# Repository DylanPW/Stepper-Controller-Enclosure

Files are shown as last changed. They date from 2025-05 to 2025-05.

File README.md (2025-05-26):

# Stepper Controller Enclosure
CAD Files & Arduino Code for a 3D Printed Enclosure for the ZK-SMC02 Stepper Driver. Features current and voltage monitoring.

Uses an Arduino Nano, 70x40 0.42" I2C LCD, ACS712 Voltage Sensor (30A in my case), and a voltage sensor module.

Voltage and current measurements were fine for my purposes but were still inaccurate compared to my multimeter. You get what you pay for.

Enclosure fits the Stepper Controller unit, and a 5x7cm proto-pcb with screw terminals, JST-XH and header pins exposed. There is a slot for a label. STEP file is included as other hardware will require remixing.

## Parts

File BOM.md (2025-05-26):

BOM

|Item|QTY|Notes|
|---|---|---|
|ZK-SMC02|1| |
|Arduino Nano w/ headers|1| |
|5x7cm 2.54mm Proto-PCB|1|Hole spacing specific to the generic green type|
|ACS712 Current Sensor|1|30A version used here, though 5A variant would suit better. Reccommend calibrating sensor regardless in the Arduino code|
|Smart Electronics DC 0-25V Voltage Sensor|1|Remove screw terminal|
|0.42" I2C OLED (72x40) SSD1306|1|Requires mounting points in the PCB|
|54x9x2mm Clear Acrylic|1|Easily replaced, adjust retainer to suit what you have.|
|KF-301 4P Terminal Block Connector|1|I used 2x 2P connectors, 4P would be better|
|JST-XH 2P Socket|1| |
|JST-XH 2P Connector & Pins|1| |
|JST-XH 4P Socket|2| |
|JST-XH 4P Right Angle Socket|1|Used for LCD, can be substituted for standard right angle header.|
|JST-XH 4P Connector & Pins|3| |
|3 pin 2.54mm header|3|Two used for voltage sensor mounting, one of those will need the center pin removed.|
|3 pin 2.54mm Female Dupont Connector & pins|2| |
|4 pin 2.54mm header|1| |
|XT60E-M|1| |
|15 pin 2.54mm Female header|2| |
|M2x6mm Self Tapping Screws|7| |
|M2x10mm Self Tapping Screws|7| |
|M2.5x6mm Machine Head Screws|2| |
|M3x4mm Machine Head Screws|2| |
|Misc Wire|1|I used 22AWG solid core for the PCB, some 18AWG for the power connections and some spare 20AWG silicone wire for anything else.|
|Ferrules for wire ends|1| |

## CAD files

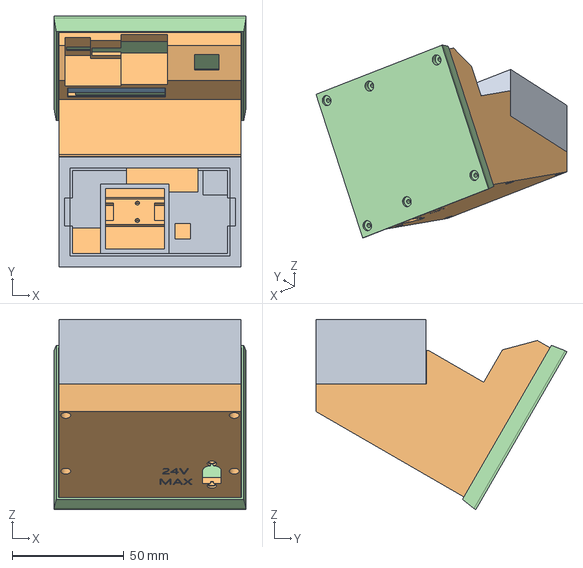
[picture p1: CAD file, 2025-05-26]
CAD/ZK-SMC02_Case.step
86.0 x 112.5 x 85.3 mm

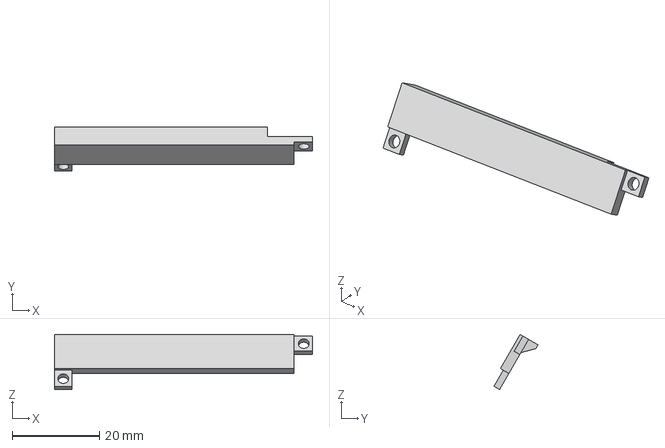
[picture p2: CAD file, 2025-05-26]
STL/LabelRetainer.3mf
59.0 x 10.1 x 12.6 mm

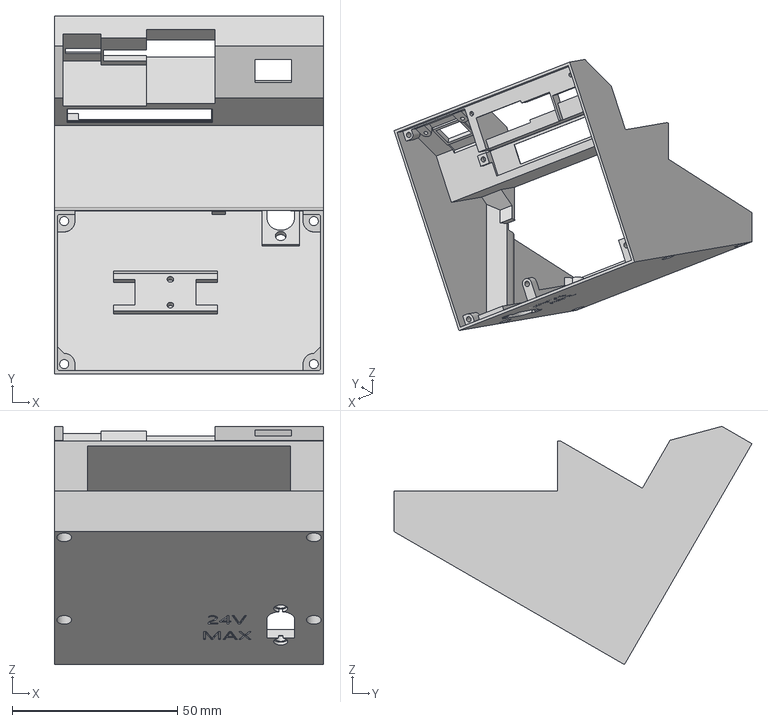
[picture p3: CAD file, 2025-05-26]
STL/Shell.3mf
81.5 x 108.3 x 72.1 mm

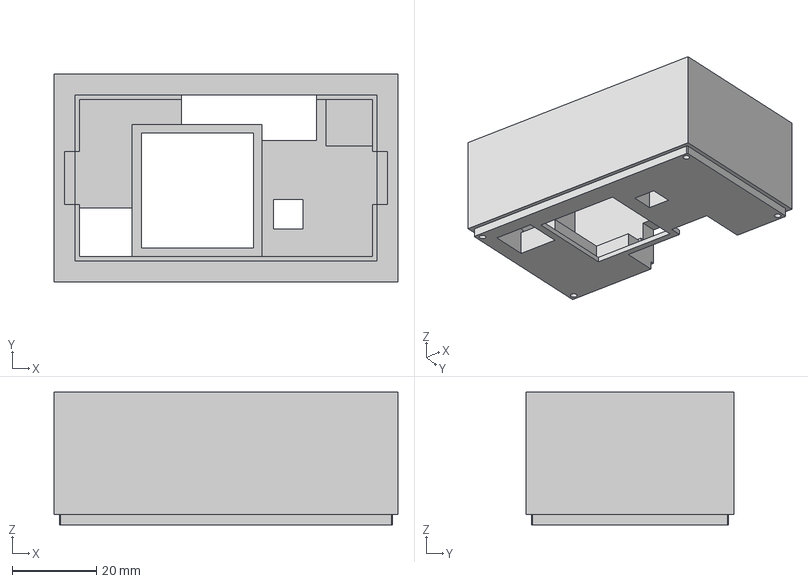
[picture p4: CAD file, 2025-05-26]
STL/Test Board Enclosure.3mf
81.5 x 49.2 x 31.5 mm

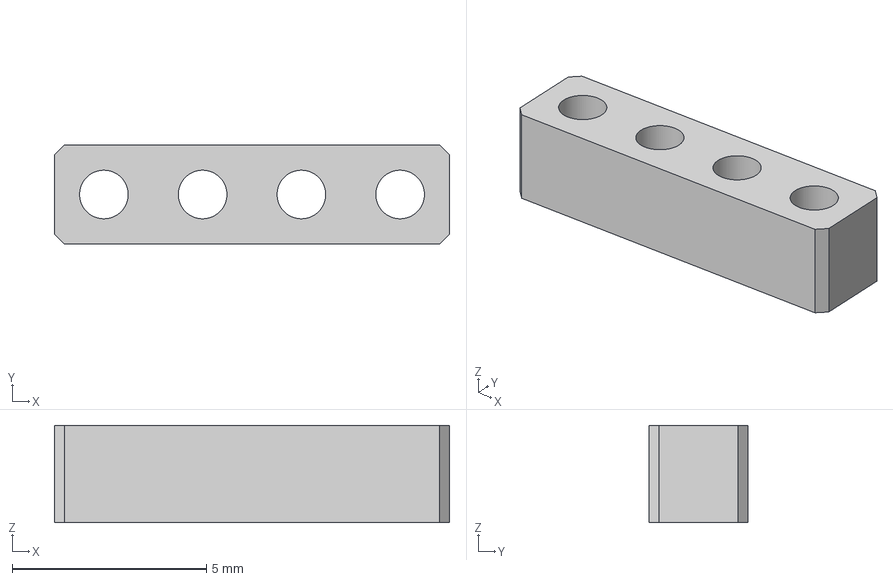
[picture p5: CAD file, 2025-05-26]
STL/DupontSpacer.3mf
10.2 x 2.54 x 2.50 mm

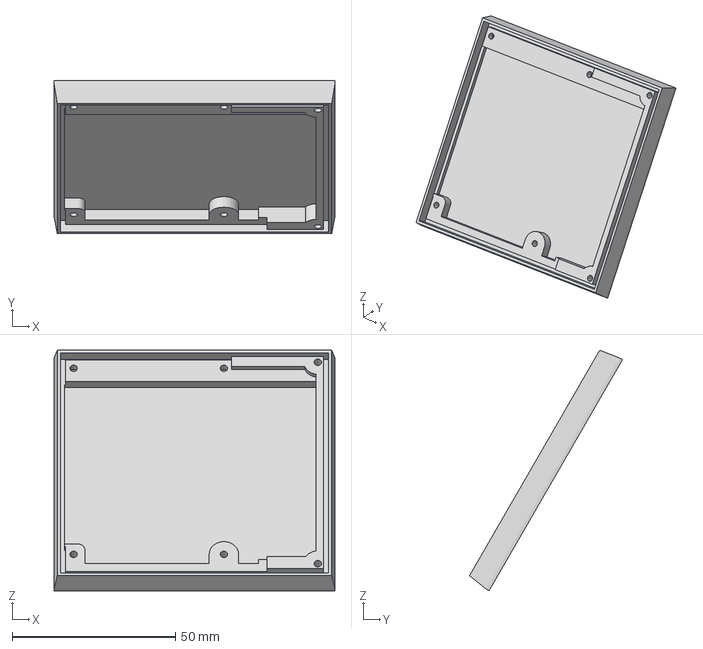
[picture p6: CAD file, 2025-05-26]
STL/Base.3mf
86.0 x 46.8 x 73.6 mm

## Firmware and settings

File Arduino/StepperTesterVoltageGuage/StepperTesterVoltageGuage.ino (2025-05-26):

#include <Wire.h>
#include <Adafruit_SSD1306.h>
#include <splash.h>
#include "PinChangeInterrupt.h" 

//display definitions; display is 70x40 ssd1306
#define SCREEN_WIDTH 128 // OLED display width, in pixels
#define SCREEN_HEIGHT 64 // OLED display height, in pixels
#define SCREEN_START_X 29
#define SCREEN_START_Y 24
#define SCREEN_REAL_WIDTH 70
#define SCREEN_REAL_HEIGHT 40
#define OLED_RESET     -1 // Reset pin # (or -1 if sharing Arduino reset pin)
#define SCREEN_ADDRESS 0x3C ///< See datasheet for Address; 0x3D for 128x64, 0x3C for 128x32
Adafruit_SSD1306 display(SCREEN_WIDTH, SCREEN_HEIGHT, &Wire, OLED_RESET);


float voltage;
float current;

int voltpin = A1;
int amppin = A0;
float multiplier = 0.222;

int sampleCount = 256;
float interval_current;

void displayValues(){
  
  display.clearDisplay();  
  display.setCursor(SCREEN_START_X, SCREEN_START_Y);
  String line = String(voltage)+"V";
  display.print(line);
  display.setCursor(SCREEN_START_X, SCREEN_START_Y + 24);
  line = String(current)+"A";
  display.print(line);
  display.display();
}

void setup()
{
	Serial.begin(9600);
  if(!display.begin(SSD1306_SWITCHCAPVCC, SCREEN_ADDRESS)) {
    Serial.println(F("SSD1306 allocation failed"));
    for(;;); // Don't proceed, loop forever
  }
  display.clearDisplay();
  display.setTextSize(2);
  display.setTextColor(SSD1306_WHITE);
  displayValues();
}

void loop()
{
	float temp;
	temp=analogRead(voltpin);
	voltage=((temp/4.105775)/10);
  
  float sensorRead = 0.0;
  float currentTemp = 0.0;
  float sampleTotal = 0.0;

  // buck converter outputs 4.96 volts
  for (int x = 0; x < sampleCount; x++){
    sensorRead = analogRead(A0)*(4.96 / 1024.0);  
    currentTemp = (((sensorRead) - (4.96/2))/multiplier);
    sampleTotal += currentTemp;
    interval_current = max(interval_current, currentTemp);
    delay(2);
  }  
  current = interval_current;
  interval_current = 0;
  displayValues();

}
